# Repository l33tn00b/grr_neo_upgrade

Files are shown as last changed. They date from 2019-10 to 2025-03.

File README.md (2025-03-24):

# grr_neo_upgrade
Upgrading the German RepRap (GRR) Neo to be a usable printer

I've been using a German RepRap Neo 3D Printer for quite a while now.
But it has somehow always left me wanting. Oozing was terrible, precision wasn't really superb. Speed sucked. But why? The mechanics are not quite rock solid but very decent. It has a metal frame and a z-axis spindle. On the other hand there are some design choices that are at best questionable. T3 pulleys and belts? The DD2 extruder, directly attached to the extruder's stepper motor (good luck with the threads, the spring load gets fed into these with hilariously short screws). No cooling fan. 

I bought the printer at a discount. It had been used as a display/demonstration unit at a local electronics market (think Best Buy). Actually, I can't remember the date, it must have been around 2015/2016. 

I feel a bit sad about the fact that German RepRap abandoned the printer. There still is a repetier firmware available on GitHub. But the last changes are from four years ago: https://github.com/GermanRepRap/Repetier-Firmware 

# Active Cooling
Pretty much a month after having bought it. That greatly improved long/thin prints.
See https://www.thingiverse.com/thing:646029

# Hotend Upgrade
The stock hotend is one of the main reasons why prints are crappy. I learned a great deal declogging it. Filament tends to get stuck because of a bad/non-existing heat break. So the filament melts up in the PTFE tube. Now, I have an E3D V6. 
See https://www.thingiverse.com/thing:971035 for the mounting parts.
Hotend assembly is at https://e3d-online.dozuki.com/Guide/V6+Assembly/6?lang=en.
You will have to shorten the belts to fit these into Kakadu's hotend mount. This is not a problem since you'll never want to return to the stock hotend.
Issues on the way were:
* Fitting the new cables (thicker heater cartridge supply cables) into the cable guide.
* The E3D's nozzle is slightly higher than the stock nozzle. Printing on 3mm glass, now (correction: Using the heated bed, it's a PEI metal plate). The additional half (or so) millimetre makes up for that.
* The Y-Endstop needs to be moved to the right. This is due to the new carriage being a bit wider. Keep the screw in its slightly rotated position towards the back of the printer. Else the carriage will collide with it but not trigger the endstop.
Update: See issues for comments from the original creator of the direct drive upgrade.

# Firmware Upgrade 
The printer comes with a repetier firmware v0.82. Nowadays, repetier is at v1.0.3. So while I was at the hotend upgrade I decided to update the firmware as well. The main reason was that I had to recompile anyway (because of the new thermistor included in the E3D v6).
Don't be fooled by E3D's "this is easy". I had to update the bootloader as well. Assuming that you already have the Arduino IDE installed and that you're in possession of a programmer...
## Firmware compilation
1) get and install teensyduino
2) compile repetier firmware for teensy++2.0 in arduino ide
3) export hex file (will be written to your sourcecode directory) (DON'T FORGET THIS AFTER CHANGING configuration.h !)
## Booloader Upgrade
1) get hid bootloader from http://blog.lincomatic.com/?p=548
2) get ready for programming (I'm using a JTAGICE3)
3) flash bootloader 
4) when done, you should see a message in the lower right corner of the screen indicating a successful installation of a HID input device :)
5) flash newly compiled firmware (assuming the firmware file is in a subfolder called "Repetier"): hid_bootloader_cli -mmcu=at90usb1286 .\Repetier\Repetier.ino.TEENSY2PP.hex (don't forget to set and remove the BOOT jumper)

See files for the configuration with the E3D v6 hotend. There also is a compiled image.
After removing the printer's back side for the nth time I decided it was time for a boot jumper extension dangling at the side. Makes firmware upgrades/changes much easier.

# Lighting
There's nothing to see, here... literally. Without additional lighting it's pretty hard to see what is going on inside the printer. The main contributing factor surely is the solid side/rear walls. So I got a cheap 12V LED stripe from aliexpress (https://www.aliexpress.com/item/32333870936.html?spm=a2g0s.9042311.0.0.27424c4dBqQZxE), cut it to size and mounted it above the front opening on 3D-printed 45° mounts. 

# Extruder Upgrade
As previously stated: The extruder is an utter piece of cr.p. To fix this, I've added a Bondtech BMG extruder. It is driven by a Trinamic stepper. There is an adapter on Thingiverse: https://www.thingiverse.com/thing:3010010
Catch is: The holes for mounting the extruder adapter do not fit the holes on Kakadu's Hotend mount. So you either do the entire thing at once with Mechanotronikum's files (including his Hotend Mount). Or you take the modified parts I'm providing here (https://github.com/l33tn00b/grr_neo_upgrade/blob/master/adapter_loecher_angepasst.stl).
Dooh. Tried to implement bed probing for mesh calibration by means of a piezo probe (yet another modification to the direct drive upgrade). Turns out that the bed has different resistance to the downward force when coming in contact with the nozzle. Viewed from the front of the printer: Left side of the bed offers less resistance that right hand side. This is obvious when turning around the printer: On the left, there is only one guide around the rod, on the right side there's two. So there is much more stability on the right hand side in terms of twisting. This printer was designed by <insert favorite insult>.  

# Various Fixes
## Printrboard Rev D
Duh. Someone please adjust the (lead free?!?) reflow solder process parameters. I've always had that strange feeling with the Micro USB jack. Guess what? It came off today. Rock solid contact for the tabs connecting +-Signal/GND/+5V. Not so much for the chassis of the jack. Luckily, only the Sense Pin's trace came off the PCB. That one wasn't connected anyway. So I spent the better half of the evening looking for my bag of USB connectors. Finally found them and soldered a new SMT USB jack onto the board. Lead, please. Somehow, I have a feeling of knowing why I usually choose through-hole USB connectors. Even when using SMT connectors, there are some that provide two little tabs that go into holes on the PCB. Much better transfer of mechanical loads when plugging/unplugging. The jack probably held such a long time only because of not being used very often: GRR's Neo uses an old-fashioned USB B type connector that is internally wired to the Micro USB jack. 

# Duet2 Wifi Upgrade
Used Mechanotronikum's excellent Duet2 Wifi board holder: https://www.myminifactory.com/object/3d-print-neodue-part-1-duet-wifi-for-grr-neo-130755

# Adjustable Z Endstop
Upgraded to inductive endstop. See https://www.thingiverse.com/thing:892356  
Use an NPN Endstop, makes life much easier. You need a BAT43 Diode for that. See https://forum.duet3d.com/topic/10596/sanity-check-plz-omron-inductive-switch-for-xyz-endstops/6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  

# Heated Bed
Don't use Bang-Bang mode. Do a PID tune.

# 24V Upgrade
The bed heater draws quite some power. See https://docs.duet3d.com/User_manual/Connecting_hardware/Heaters_bed  
So everything runs on 24V, now. Duet board, Hotend heater cartridge, Bed heater. Power is supplied from a Meanwell LRS-350-24. Alternate is Meanwell GST220A24-R76. Re-Did the power supply PCB

# To Do
* Done: Adjustable Z axis end switch. The stock one is calibrated to a printing bed height that is based on 2mm PMMA plus BuildTak. I now print on glass which fits nicely with the E3D V6's slightly higher nozzle..
* Done: Heated Bed (parts are here) to prevent warping when printing on glass. Plus finally printing material other than PLA. See https://github.com/l33tn00b/grr_neo_upgrade/blob/master/halterung_druckbett_2%20v1.step for a sketch of the mounting adapter for classic 4-point mounting of a heated print bed.
* Done: Replace Printrboard (Duet3D WiFi is on its way).
* Replace T3 belts and pulleys with standard T2.5 (distant future. Parts are here, though).

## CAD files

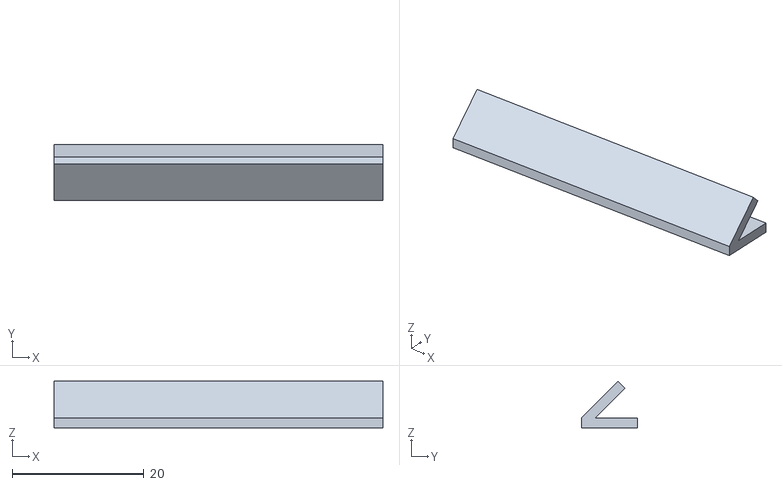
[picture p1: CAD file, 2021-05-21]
schiene_45grad5cm.stl
50.0 x 8.50 x 7.07

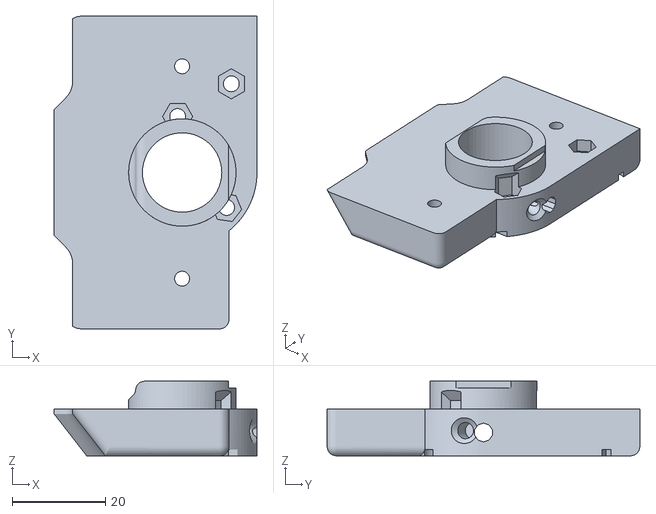
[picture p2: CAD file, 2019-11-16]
adapter_loecher_angepasst.stl
43.5 x 67.0 x 16.0

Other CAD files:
halterung_druckbett_2 v1.step

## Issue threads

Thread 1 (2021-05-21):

Piezo-Sensorik und Link

Braintoe, 2021-05-21:
Moin, ich bin einfach mal so dreist und schreib hier auf Deutsch:

Erstmal schön, daß mein Bondtech-Adapter für Kakadus Druckkopf so gut ankommt :-) Daß ich bein Einbau meiner Kugellager für die Zahnriemen die Bohrungen im Druckkopf-Körper versetzt hatte, hatte ich ja vollkommen vergessen - ich ergänze da noch einen Hinweis und aktualisiere die Datei.. Ansonsten ist das komplette Set auf MyMinifactory zu finden  ( https://www.myminifactory.com/users/Mechanotronikum )

Zu der Piezo-Problematik: Unter https://forum.duet3d.com/topic/14477/piezo-board-with-4-sensors/29  und https://forum.duet3d.com/topic/22547/two-precision-piezo-boards-in-parallel-on-one-input-possible/ hab ich mein Setup beschrieben. Vielleicht hilft das weiter ;-)

Viele Grüße!

l33tn00b, 2021-05-21:
Hi,

Danke für die Hinweise, ganz besonders auch zur Piezo-Problematik!
Mir wars irgendwann zu dumm und ich habe "einfach" ein neues Blech als Adapter für eine traditionelle Montage mit vier Schrauben Lasern lassen. :P Den Entwurf dafür stelle ich auch mal noch ins Repo...

Auch die Variante mit Piezo-Disc in der Halterung fürs Hotend habe ich mal ausprobiert. Das gibt einigermaßen brauchbare Signale.. Ein Neo läuft jetzt damit. Nach den STLs dafür muss ich mal noch suchen...

Viele Grüße!

Braintoe, 2021-05-22:
Oha. Den Piezo im Druckkopf hab auch überlegt - und dann verworfen. Ohne Kakadus Desing völlig über den Haufen zu werfen, wußte ich keinen Weg, den da reinzubasteln. Da bin ich mal gespannt, wie das aussieht.

Das Böech wäre auch meine Lösung gewesen, wenn meine Bastelei nicht geklappt hätte. So bin cih aber darum herumgekommen ;-)

Ach so - noch ein Tip: nach meine Erfahrung hält die Duet von den originalen Motoren für X und Y nicht besonders viel - sobald man die etwas schneller laufen läßt (was die Duet problemlos schafft), versetzen die Dinger den ganzen Drucker in Schwingungen. Ich hab damals _lange_ mit den Motortreiber-Einstellungen herumgefuhrwerkt, um diese elendigen Vibrationen loszuwerden, nachdem auch Wechsel der ganzen Wellen und Linearlager gegen Misumi-Teile nix genutzt hat - und dann die Stepper für X und Y gegen 14HS13-0804 von omc-stepperonline.com getauscht. Die laufen um ein Vielfaches sanfter als die originalen Motoren von GRR.
Mittlerweile habe die sich meine damalige Anfrage zu Herzen genommen und es gibt diese Motoren da auch mit Dual Shaft, so daß man nicht mehr gar so viel basteln muß, um den Motor für die X-Achse zu tauschen (bei mir werkelt da noch die Variante mit hohlem Schaft, für die ich mir erst eine Welle für die Motorrückseite drehen und einpressen mußte...)

l33tn00b, 2021-05-22:
So, da habe ich mal einen Screenshot von meiner Konstruktion mit Platz für eine Piezo-Disc und den E3D Filament Monitor. Ist eine üble Bastelei und hat eine enorme Bauhöhe, was dann einen ziemlich langen Hebel macht. Schnell fahren ist da nicht 👎
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

Ja, es ist schon schön, wenn man sich mal über die Kiste austauschen kann. Eigentlich ist die Mechanik ja wirklich nicht schlecht, das Gehäuse ist echt solide und kein Vergleich mit so wackeligen Konstruktionen mit nur einem senkrechten Profil und dem Bett das dann untendrunter hin und her fährt (Hallo Ender...).

Zum Tausch der Motoren bin ich noch nicht gekommen. Danke für den Tip mit Stepperonline, da habe ich bei Amazon bisher gemischte Rezensionen gelesen und war iummer etwas vorsichtig. Das erklärt auch den riesigen Aufbau auf der x-Achse :P Dort habe ich einen Trinamic-Motor an den BMG rangebaut. Schiebt und schiebt und schiebt das Filament gnadenlos *g*

Ich mache Mechanik eher nebenher, meine Metallbearbeitungsmöglichkeiten sind etwas eingeschränkt, drehen ist nicht... Insofern echt Hut ab für "ich drehe mir mal 'ne Achse und presse die selber ein" :)

Braintoe, 2021-05-26:
Oha - ja, das Teil ist wuchtig... daher habe ich meinen Filamentsensor (der China-Klotz von BigTreeTech von AliExpress, geht aber zuverlässig, das Ding) hinten direkt über die Filamentrolle an den Eingang vom Bowden gehängt. Bei den paar Zentimetern zwischen Extruder und Hotend sehe ich das Risiko, daß was passiert, als gleich Null an - und alles andere erkennt der auch da ausreichend genau.

Den Bondtech befeuere ich mit einem 17HS08, auch von Stepperonline, nachdem ich keinen noch kleineren Nema17-Schrittmotor mit ausreichend langer Achse gefunden hatte. Der reicht bei der hohen Untersetzung des Bondtech aber völlig aus, um das Filament im Fall des Falls eher zu zerfräsen als Schritte zu überspringen :-)
Mittlerweile gibts die Dinger von Stepperonline ja sogar mit Versand aus Deutschland, sehe ich grad.

So Kleinkram kann ich drehen, seit ich vor einiger Zeit mal eine Unimat bei Ebay billig geschossen habe. Die ist für sowas echt Gold wert. Der Friedhofssteinmetz war zwar etwas verwirrt, als ich ihm die Skizze für die kleine Granitplatte zum Draufmontieren gezeigt hab, aber er hat sie anstandslos gemacht ;-)

Woran ich mich aber noch nicht getraut hab, ist die Zahnriemen zu wechseln - mit dem Thema habe ich mich bisher schlicht noch nicht befaßt (ein Fall von "läuft- ist gut" - die ungehärteten Achsen und die Linearlager waren bei meinem Neo da wesentlich dringender, da bei denen wohl das Fett vergessen wurde...). Mal dumm gefragt: was haben die T2,5-Riemen denn für Vorteile gegenüber den HTD3M des Neo? Wenn mein in dieser Hinsicht ziemlich rostiges Wissen (bitte nicht drauf festnageln) noch stimmt, hat das T-Profil mehr Spiel als das HTD-Profil, was ich beim 3D-Drucker eher als unschön empfinden würde...

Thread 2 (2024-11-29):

Hotend

nstsaby, 2024-11-29:
Hy, the hotend is 12v or 24?
Thanks

l33tn00b, 2024-11-29:
Either one will fit. It depends on your supply voltage. In the end, I used the 24V version because of the heated bed. Which wasn't much of a problem once the PrintrBoard had been replaced by a Duet2 Board capable of handling 24V.

Am 29. November 2024 08:37:25 UTC schrieb nstsaby ***@***.***>:
>Hy, the hotend is 12v or 24?
>Thanks
>

nstsaby, 2024-11-29:
Means the neo is stock 12v?

l33tn00b, 2024-11-29:
Yup. 12V 20W heater cartridge.

Am 29. November 2024 10:36:39 UTC schrieb nstsaby ***@***.***>:
>Means the neo is stock 12v?
>

nstsaby, 2024-11-30:
Thanks

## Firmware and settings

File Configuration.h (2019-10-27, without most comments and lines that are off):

#define CONFIGURATION_H
#define NUM_EXTRUDER 1
#define MOTHERBOARD 9
#include "pins.h"
#undef FAN_BOARD_PIN
#define FAN_BOARD_PIN -1
#define BOARD_FAN_SPEED 255
#define BOARD_FAN_MIN_SPEED 0
#define FAN_THERMO_PIN -1
#define FAN_THERMO_MIN_PWM 128
#define FAN_THERMO_MAX_PWM 255
#define FAN_THERMO_MIN_TEMP 45
#define FAN_THERMO_MAX_TEMP 60
#define FAN_THERMO_THERMISTOR_PIN -1
#define FAN_THERMO_THERMISTOR_TYPE 1
#define BLUETOOTH_SERIAL  -1
#define BLUETOOTH_BAUD  115200
#define MIXING_EXTRUDER 0
#define DRIVE_SYSTEM 0
#define XAXIS_STEPS_PER_MM 76.20
#define YAXIS_STEPS_PER_MM 88.88
#define ZAXIS_STEPS_PER_MM 3200.00
#define EXTRUDER_FAN_COOL_TEMP 50
#define PDM_FOR_EXTRUDER 0
#define PDM_FOR_COOLER 0
#define DECOUPLING_TEST_MAX_HOLD_VARIANCE 20
#define DECOUPLING_TEST_MIN_TEMP_RISE 1
#define KILL_IF_SENSOR_DEFECT 0
#define RETRACT_ON_PAUSE 2
#define PAUSE_START_COMMANDS ""
#define PAUSE_END_COMMANDS ""
#define SHARED_EXTRUDER_HEATER 0
#define EXT0_X_OFFSET 0
#define EXT0_Y_OFFSET 0
#define EXT0_Z_OFFSET 0
#define EXT0_STEPS_PER_MM 130.00
#define EXT0_TEMPSENSOR_TYPE 8 //fuer e3dv6 hotend statt dem original
#define EXT0_TEMPSENSOR_PIN TEMP_0_PIN
#define EXT0_HEATER_PIN HEATER_0_PIN
#define EXT0_STEP_PIN ORIG_E0_STEP_PIN
#define EXT0_DIR_PIN ORIG_E0_DIR_PIN
#define EXT0_INVERSE 1 //in der original fw "true"
#define EXT0_ENABLE_PIN ORIG_E0_ENABLE_PIN
#define EXT0_ENABLE_ON 0
#define EXT0_MIRROR_STEPPER 0
#define EXT0_STEP2_PIN ORIG_E0_STEP_PIN
#define EXT0_DIR2_PIN ORIG_E0_DIR_PIN
#define EXT0_INVERSE2 0
#define EXT0_ENABLE2_PIN ORIG_E0_ENABLE_PIN
#define EXT0_MAX_FEEDRATE 30
#define EXT0_MAX_START_FEEDRATE 10
#define EXT0_MAX_ACCELERATION 4000
#define EXT0_HEAT_MANAGER 1
#define EXT0_PREHEAT_TEMP 190
#define EXT0_WATCHPERIOD 1
#define EXT0_PID_INTEGRAL_DRIVE_MAX 130
#define EXT0_PID_INTEGRAL_DRIVE_MIN 60
#define EXT0_PID_PGAIN_OR_DEAD_TIME 2.38 //PID Werte sind aus dem autotune
#define EXT0_PID_I 0.01
#define EXT0_PID_D 62.89
#define EXT0_PID_MAX 70
#define EXT0_ADVANCE_K 0
#define EXT0_ADVANCE_L 0
#define EXT0_ADVANCE_BACKLASH_STEPS 0
#define EXT0_WAIT_RETRACT_TEMP 150
#define EXT0_WAIT_RETRACT_UNITS 0
#define EXT0_SELECT_COMMANDS "M120 S5 P5\nM117 Extruder 1"
#define EXT0_DESELECT_COMMANDS ""
#define EXT0_EXTRUDER_COOLER_PIN -1
#define EXT0_EXTRUDER_COOLER_SPEED 255
#define EXT0_DECOUPLE_TEST_PERIOD 12000
#define EXT0_JAM_PIN -1
#define EXT0_JAM_PULLUP 0
#define FEATURE_RETRACTION 1
#define AUTORETRACT_ENABLED 0
#define RETRACTION_LENGTH 3
#define RETRACTION_LONG_LENGTH 13
#define RETRACTION_SPEED 40
#define RETRACTION_Z_LIFT 0
#define RETRACTION_UNDO_EXTRA_LENGTH 0
#define RETRACTION_UNDO_EXTRA_LONG_LENGTH 0
#define RETRACTION_UNDO_SPEED 20
#define FILAMENTCHANGE_X_POS 0
#define FILAMENTCHANGE_Y_POS 0
#define FILAMENTCHANGE_Z_ADD  2
#define FILAMENTCHANGE_REHOME 1
#define FILAMENTCHANGE_SHORTRETRACT 5
#define FILAMENTCHANGE_LONGRETRACT 50
#define JAM_METHOD 1
#define JAM_STEPS 220
#define JAM_SLOWDOWN_STEPS 320
#define JAM_SLOWDOWN_TO 70
#define JAM_ERROR_STEPS 500
#define JAM_MIN_STEPS 10
#define JAM_ACTION 1
#define RETRACT_DURING_HEATUP true
#define PID_CONTROL_RANGE 15
#define SKIP_M109_IF_WITHIN 2
#define SCALE_PID_TO_MAX 0
#define EXTRUDE_MAXLENGTH 160
#define NUM_TEMPS_USERTHERMISTOR0 0
#define USER_THERMISTORTABLE0 {}
#define NUM_TEMPS_USERTHERMISTOR1 0
#define USER_THERMISTORTABLE1 {}
#define NUM_TEMPS_USERTHERMISTOR2 0
#define USER_THERMISTORTABLE2 {}
#define GENERIC_THERM_VREF 5
#define GENERIC_THERM_NUM_ENTRIES 33
#define HEATER_PWM_SPEED 0
#define COOLER_PWM_SPEED 0
#define HAVE_HEATED_BED 0
#define HEATED_BED_PREHEAT_TEMP 55
#define HEATED_BED_MAX_TEMP 120
#define SKIP_M190_IF_WITHIN 3
#define HEATED_BED_SENSOR_TYPE 1
#define HEATED_BED_SENSOR_PIN TEMP_1_PIN
#define HEATED_BED_HEATER_PIN HEATER_1_PIN
#define HEATED_BED_SET_INTERVAL 5000
#define HEATED_BED_HEAT_MANAGER 0
#define HEATED_BED_PID_INTEGRAL_DRIVE_MAX 255
#define HEATED_BED_PID_INTEGRAL_DRIVE_MIN 80
#define HEATED_BED_PID_PGAIN_OR_DEAD_TIME   196
#define HEATED_BED_PID_IGAIN   33
#define HEATED_BED_PID_DGAIN 290
#define HEATED_BED_PID_MAX 255
#define HEATED_BED_DECOUPLE_TEST_PERIOD 300000
#define MIN_EXTRUDER_TEMP 150
#define MAXTEMP 285
#define MIN_DEFECT_TEMPERATURE 5
#define MAX_DEFECT_TEMPERATURE 290
#define MILLISECONDS_PREHEAT_TIME 30000
#define SUPPORT_LASER 0
#define LASER_PIN -1
#define LASER_ON_HIGH 1
#define LASER_WARMUP_TIME 0
#define LASER_PWM_MAX 255
#define LASER_WATT 2
#define SUPPORT_CNC 0
#define CNC_WAIT_ON_ENABLE 300
#define CNC_WAIT_ON_DISABLE 0
#define CNC_ENABLE_PIN -1
#define CNC_ENABLE_WITH 1
#define CNC_DIRECTION_PIN -1
#define CNC_DIRECTION_CW 1
#define CNC_PWM_MAX 255
#define CNC_RPM_MAX 8000
#define CNC_SAFE_Z 150
#define DEFAULT_PRINTER_MODE 0
#define MULTI_ZENDSTOP_HOMING 0
#define ENDSTOP_PULLUP_X_MIN true
#define ENDSTOP_X_MIN_INVERTING false
#define MIN_HARDWARE_ENDSTOP_X true
#define ENDSTOP_PULLUP_Y_MIN true
#define ENDSTOP_Y_MIN_INVERTING false
#define MIN_HARDWARE_ENDSTOP_Y true
#define ENDSTOP_PULLUP_Z_MIN true
#define ENDSTOP_Z_MIN_INVERTING false
#define MIN_HARDWARE_ENDSTOP_Z true
#define ENDSTOP_PULLUP_Z2_MINMAX true
#define ENDSTOP_Z2_MINMAX_INVERTING false
#define MINMAX_HARDWARE_ENDSTOP_Z2 false
#define ENDSTOP_PULLUP_X_MAX true
#define ENDSTOP_X_MAX_INVERTING false
#define MAX_HARDWARE_ENDSTOP_X false
#define ENDSTOP_PULLUP_Y_MAX true
#define ENDSTOP_Y_MAX_INVERTING false
#define MAX_HARDWARE_ENDSTOP_Y false
#define ENDSTOP_PULLUP_Z_MAX true
#define ENDSTOP_Z_MAX_INVERTING false
#define MAX_HARDWARE_ENDSTOP_Z false
#define ENDSTOP_PULLUP_X2_MIN true
#define ENDSTOP_PULLUP_Y2_MIN true
#define ENDSTOP_PULLUP_Z2_MINMAX true
#define ENDSTOP_PULLUP_X2_MAX true
#define ENDSTOP_PULLUP_Y2_MAX true
#define ENDSTOP_X2_MIN_INVERTING false
#define ENDSTOP_Y2_MIN_INVERTING false
#define ENDSTOP_X2_MAX_INVERTING false
#define ENDSTOP_Y2_MAX_INVERTING false
#define MIN_HARDWARE_ENDSTOP_X2 false
#define MIN_HARDWARE_ENDSTOP_Y2 false
#define MAX_HARDWARE_ENDSTOP_X2 false
#define MAX_HARDWARE_ENDSTOP_Y2 false
#define X2_MIN_PIN -1
#define X2_MAX_PIN -1
#define Y2_MIN_PIN -1
#define Y2_MAX_PIN -1
#define Z2_MINMAX_PIN -1
#define max_software_endstop_r true
#define min_software_endstop_x true
#define min_software_endstop_y true
#define min_software_endstop_z true
#define max_software_endstop_x true
#define max_software_endstop_y true
#define max_software_endstop_z true
#define DOOR_PIN -1
#define DOOR_PULLUP 1
#define DOOR_INVERTING 1
#define ENDSTOP_X_BACK_MOVE 5
#define ENDSTOP_Y_BACK_MOVE 5
#define ENDSTOP_Z_BACK_MOVE 2
#define ENDSTOP_X_RETEST_REDUCTION_FACTOR 2
#define ENDSTOP_Y_RETEST_REDUCTION_FACTOR 2
#define ENDSTOP_Z_RETEST_REDUCTION_FACTOR 2
#define ENDSTOP_X_BACK_ON_HOME 1
#define ENDSTOP_Y_BACK_ON_HOME 14
#define ENDSTOP_Z_BACK_ON_HOME 0
#define ALWAYS_CHECK_ENDSTOPS 0
#define MOVE_X_WHEN_HOMED 0
#define MOVE_Y_WHEN_HOMED 0
#define MOVE_Z_WHEN_HOMED 0
#define X_ENABLE_ON 0
#define Y_ENABLE_ON 0
#define Z_ENABLE_ON 0
#define DISABLE_X 0
#define DISABLE_Y 0
#define DISABLE_Z 0
#define DISABLE_E 0
#define INVERT_X_DIR 0
#define INVERT_X2_DIR 0
#define INVERT_Y_DIR 0
#define INVERT_Y2_DIR 0
#define INVERT_Z_DIR 1 //true in der orig fw
#define INVERT_Z2_DIR 0
#define INVERT_Z3_DIR 0
#define INVERT_Z4_DIR 0
#define X_HOME_DIR -1
#define Y_HOME_DIR -1
#define Z_HOME_DIR -1
#define X_MAX_LENGTH 150
#define Y_MAX_LENGTH 150
#define Z_MAX_LENGTH 150
#define X_MIN_POS 0
#define Y_MIN_POS 0
#define Z_MIN_POS 0
#define PARK_POSITION_X 0
#define PARK_POSITION_Y 10
#define PARK_POSITION_Z_RAISE 10
#define DISTORTION_CORRECTION 0
#define DISTORTION_CORRECTION_POINTS 5
#define DISTORTION_LIMIT_TO 2
#define DISTORTION_CORRECTION_R 100
#define DISTORTION_PERMANENT 1
#define DISTORTION_UPDATE_FREQUENCY 15
#define DISTORTION_START_DEGRADE 0.5
#define DISTORTION_END_HEIGHT 1
#define DISTORTION_EXTRAPOLATE_CORNERS 0
#define DISTORTION_XMIN 10
#define DISTORTION_YMIN 10
#define DISTORTION_XMAX 190
#define DISTORTION_YMAX 190
#define FEATURE_BABYSTEPPING 1
#define BABYSTEP_MULTIPLICATOR 1
#define DELTA_SEGMENTS_PER_SECOND_PRINT 180 // Move accurate setting for print moves
#define DELTA_SEGMENTS_PER_SECOND_MOVE 70 // Less accurate setting for other moves
#define EXACT_DELTA_MOVES 1
#define DELTA_HOME_ON_POWER 0
#define DELTASEGMENTS_PER_PRINTLINE 20
#define STEPPER_INACTIVE_TIME 120L
#define MAX_INACTIVE_TIME 0L
#define MAX_FEEDRATE_X 4000
#define MAX_FEEDRATE_Y 4000
#define MAX_FEEDRATE_Z 30
#define HOMING_FEEDRATE_X 30
#define HOMING_FEEDRATE_Y 30
#define HOMING_FEEDRATE_Z 4
#define HOMING_ORDER HOME_ORDER_ZXY
#define ZHOME_PRE_RAISE 0
#define ZHOME_PRE_RAISE_DISTANCE 10
#define RAISE_Z_ON_TOOLCHANGE 0
#define ZHOME_MIN_TEMPERATURE 0
#define ZHOME_HEAT_ALL 1
#define ZHOME_HEAT_HEIGHT 20
#define ZHOME_X_POS 999999
#define ZHOME_Y_POS 999999
#define ENABLE_BACKLASH_COMPENSATION 0
#define X_BACKLASH 0
#define Y_BACKLASH 0
#define Z_BACKLASH 0
#define RAMP_ACCELERATION 1
#define STEPPER_HIGH_DELAY 0
#define DIRECTION_DELAY 0
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

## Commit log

2021-05-21 Add files via upload
    Print bed frame replacement. The stock one uses three mounting holes for bed mouting/leveling. This one has four holes.
2021-05-21 Add files via upload
    45 degree angle mount for led strips. just tack it to the frame using some double sided tape.
    [schiene_45grad5cm.stl]
2021-05-21 Add files via upload
    Bed Mount Adapter for "traditional" 4 screw mouting
    [halterung_druckbett_2 v1.step]

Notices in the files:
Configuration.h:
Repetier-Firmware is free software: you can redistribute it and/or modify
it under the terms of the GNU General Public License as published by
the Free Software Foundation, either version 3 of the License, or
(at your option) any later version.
